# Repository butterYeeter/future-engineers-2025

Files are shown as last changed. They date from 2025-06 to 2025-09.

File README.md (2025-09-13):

# Future Engineers 2025

Welcome to T.M.F.E.'s github for 2025

## A photo of the team with their robot:

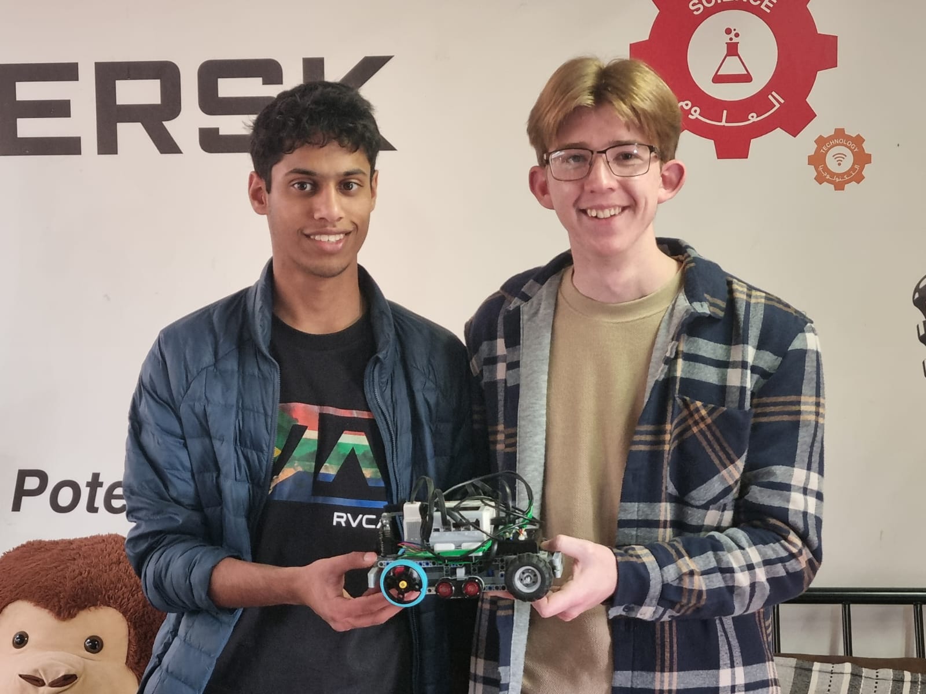
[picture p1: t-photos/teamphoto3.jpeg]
Team Photo


---

## 👥 Team Information

- **Team Name:** T.M.F.E (Trust Me I'm a Future Engineer)
- **Team Members:** Raaid, Josua, HueBert the robot

---

## 📑 Contents

* 🚗 [**Mobility Management**](#-mobility-management)
    * 🛠️ [Chassis Design](#️-chassis-design)
    * 📷 [Camera Position](#-camera-position)
    * 🚦 [Color Sensor Position](#-color-sensor-position)
    * 🧭 [Gyro Sensor Position](#-gyro-sensor-position)
    * ⚙️ [Motor Selection](#️-motor-selection)
* 🔋 [**Power & Sense Management**](#-power--sense-management)
    * 🔌 [Power Management](#-power-management)
    * 👀 [Sense Management](#-sense-management)
* 🚧 [**Obstacle Management**](#-obstacle-management)
    * 🖲️ [Sensor Polling](#-sensor-polling)
    * 🎯 [Steering Control](#-steering-control)
    * 👁 [Detection Method](#-detection-method)
    * 🔀 [Bypassing Obstacles](#-bypassing-obstacles)
    * 🧱 ["L"-shaped turn](#-l-shaped-turn)
    * 🅿️ [Parking](#🅿️-parking)
* 📸 [**Pictures**](#-pictures)
    * 🤖 [Robot Photos](#-robot-photos)
    * 👥 [Team Photos](#-team-photos)
* 🎥 [**Performance Videos**](#-performance-videos)
* 📝 [**Evaluation for Future Development**](#-evaluation-for-future-development)
    * 🤖 [Hardware Evaluation](#-hardware-evaluation)
    * 💾 [Software Evaluation](#-software-evaluation)
* ☎ [**Contact Us**](#-contact-us)
---

## 🚗 [Mobility Management](#-contents)

### 🛠️ [Chassis Design](#-contents)

- **Materials / Kits Used:**
    
    Our robot design consist mostly of original LEGO parts from the EV3 set, in addition to an external Raspberry Pi Pico microcontroller and other electronic sensors. The build instructions including the bill of materials for the LEGO part of the build can be found [here](other/Huebert_Build_Instructions_v1.pdf).
    
    We used LEGO for the construction of the chassis, because it is really easy to build with and modify. For non LEGO parts like the microcontroller circuit and color sensor, we designed and 3D printed LEGO-compatible mounts using black ABS filament to integrate with the robot chassis. The models of these mounts can be found [here](models).
    
- **Design Approach:**
    
    From prior experience, we wanted to have a small and highly maneuverable robot. We started off by listing some requirements. This included minimizing the wheelbase and track width, making the chassis compact and having sharp turning.
    
- **Wheels:** 
    
    We decided on using medium sized wheels,  having wider back wheels for better grip while driving, and thinner wheels to reduce contact area while maintaining friction.

- **Weight Distribution:**
    
    Most of the weight is centered between the front and rear wheels to maintain reliable contact with the mat at any point.
    
- **Component Placement**

    We mounted the raspberry pi on a protoboard and made a 3D printed LEGO compatible mount for it. The mount was designed to fit the robot and not the other way around. We added ports on the protoboard with wires that connect to the various components.
    
- **Steering Geometry:**
    
    Originally we opted for a standard parallel linkage steering mechanism, but when turning sharply found that the front wheels were slipping. We then modified the steering geometry to closely resemble ackermann steering.
    
- **Drivetrain:**
    
    The robot is driven using a LEGO medium motor connected to a differential gearbox system. The resulting gear ratio is 1.4:1.

### 📷 [Camera Position](#-contents)
We used a pixy cam v2 that does obstacle detection for us. 

- **Height & Angle:**
    
    We opted to position the camera on the front of the robot. It was mostly for our convenience in mounting it on the robot where there was space, but we later found it to make our lives more difficult in coding. A future improvement would be to take the angle and position of the camera into account to optimize usage of that glorious 80 degree field of view.
    
### 🚦 [Color Sensor Position](#-contents)
- We used a TCS34725 color sensor board for detecting colors on the mat. The position of the color sensor was carefully determined to maximize the accuracy of the detected colors. To achieve this we placed the color sensor at a specific height above the mat and centered it in the middle of the steering mechanism by designing a custom LEGO compatible mount. This resulted in accurate readings 

### 🧭 [Gyro Sensor Position](#-contents)
- We used an MPU6050 inertial measurement unit as our gyro sensor. The gyro sensor was mounted on a protoboard near the raspberry pi pico to make the wiring easy. We also found that placing the sensor near the center of the robot wasn't necessary due to the size of the robot. 

### ⚙️ [Motor Selection](#-contents)

- **Motor Types:**
    
    We decided on using the LEGO medium motors for both driving and steering.
- **Reason for Choice:**
    
    The LEGO medium motors are already a part of the LEGO brick system and work well with the EV3 controller. They provide a sufficient amount of torque for driving and steering the robot. They also consume less power than the large motors, which significantly increases battery life. They also have a faster speed than the large motors which is beneficial for us since our differential gearbox significantly reduces our speed.
---

## 🔋 [Power & Sense Management](#-contents)

### 🔌 [Power Management](#-contents)
To power our robot, we use a LEGO Li-on battery pack that powers the EV3. All of the LEGO sensors and motors receive power via the ports of the EV3. The Raspberry Pi Pico, is also connected to the EV3 via one of its ports. This port provides power to the Pico. All of the devices connected to the input ports receive +5V while the motors receive up to +9V.

#### **Power Diagram of EV3**
Power distribution

The pico then has it's own regulated 3.3V output that it supply's to the IMU and color sensor. (Wiring diagram for pico and sensors)

- **Core Controller:**
    
    LEGO EV3
- **Secondary Controller:**
    
    Raspberry Pi Pico
- **Battery Type:**
    
    LEGO 2200mAh 7.4V Li-ion battery pack
- **Energy Distribution:**
    
    We use a combination of LEGO cables and custom cables with RJ12 ports to integrate the pi and other sensors with the EV3 brick.
- **Monitoring Features:**
    
    The EV3 screen displays the current battery voltage so we know when it needs to be replaced and recharged.
### 👀 [Sense Management](#-contents)

- **Sensors Used:**
    |Sensor (click for buy link)|Quantity Used|What it looks like|
    |:---|:---:|:---:|
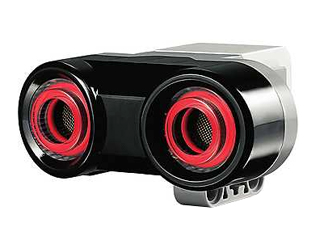
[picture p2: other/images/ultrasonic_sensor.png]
LEGO Mindsorms Ultrasonic Sensor
    [LEGO mindstorms ultrasonic sensor](https://www.bricklink.com/v2/catalog/catalogitem.page?S=45504-1#T=S&O={%22iconly%22:0}) | 2 |
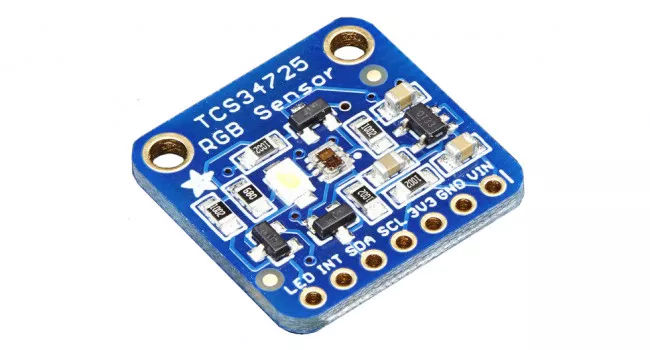
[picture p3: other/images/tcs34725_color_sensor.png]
TCS34725 Color Sensor
    [TCS34725 color sensor](https://www.robotics.org.za/AF1334?search=TCS34725)              | 1 |
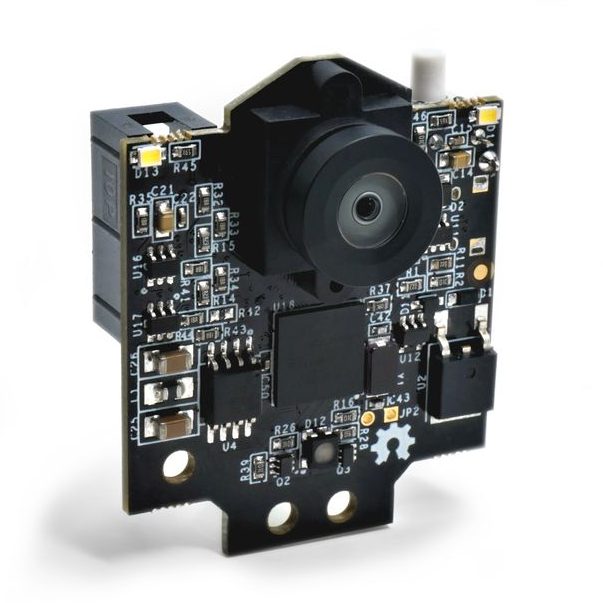
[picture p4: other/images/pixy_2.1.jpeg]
Pixycam 2.1
    [Pixycam 2.1](https://tribotix.com/product/pixycam2-1/)                        | 1 |
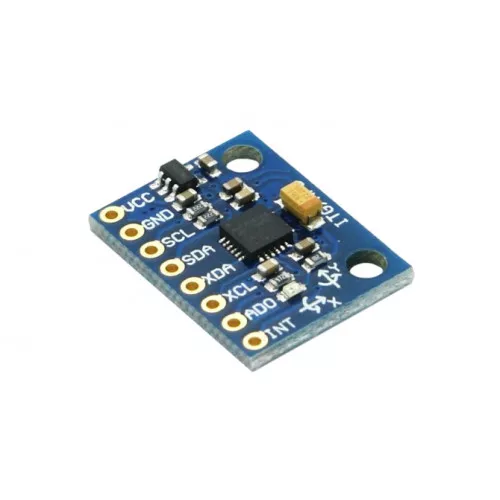
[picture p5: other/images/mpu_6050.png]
MPU 6050
    [MPU 6050 inertial measurement unit](https://www.robotics.org.za/GY-521) | 1 |
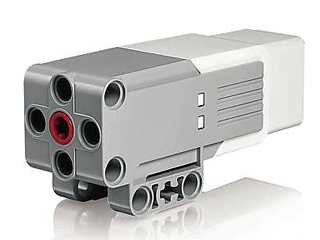
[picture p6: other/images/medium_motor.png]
LEGO Medium Motor
    [Built-in rotary encoders of the LEGO medium motors](https://www.bricklink.com/v2/catalog/catalogitem.page?S=45503-1#T=S&O={%22iconly%22:0})|2|
- **Purpose of Each Sensor:**
    - The **ultrasonic sensors** are used to recenter the robot within each straight section on the mat. We have found that the LEGO ultrasonic sensors' distance values lag behind reality. This means we can't rely on them to detect when to turn for example(by checking for when the inside wall disappears). In future we will probably switch to using time of flight sensors or even a scanning LIDAR.
    
    - The **color sensor** is used to detect the colored lines on the mat to decide when to turn. Initially we used a HiTechnic color sensor however it was quickly found to inadequate. It could not detect the colors in the short amount of time when driving over a line.

        The TCS34725 sensor returns color in the form of RGB. In order to detect orange and blue lines, we convert this color to HSV(Hue, Saturation, Value) and then simply check for a range of values for H, S and V.

        The following algorithm is used to convert RGB to HSV:

        ```C
        // Find min and max component
        float max = r;
        if (g > max) max = g;
        if (b > max) max = b;

        float min = r;
        if (g < min) min = g;
        if (b < min) min = b;

        // Calculate difference between min and max channel
        float delta = max - min;

        float h = 0.0f;
        float s = 0.0f;
        float v = max;
    
        // Determine values for saturation and hue
        if (delta > 0.00001f) {
            s = (max > 0.0f) ? (delta / max) : 0.0f;

            if (max == r) {
                h = 60.0f * ((g - b) / delta);
                if (h < 0.0f) h += 360.0f;
            } else if (max == g) {
                h = 60.0f * (((b - r) / delta) + 2.0f);
            } else {
                h = 60.0f * (((r - g) / delta) + 4.0f);
            }
        }
        ```
        
        Then we check for orange and blue using the following:
        ```C!
        // Check thresholds for blue and orange colors
        if (s > 0.35f && v > 0.6f) {
            // Blue range
            if (h >= 200.0f && h <= 250.0f) {   // Hue range for blue
                return COLOR_BLUE;
            }
        } else if (s > 0.45f && v > 0.7f) {
            if ((h >= 0.0f && h <= 50.0f) || (h >= 340.0f && h <= 360.0f)) {    // Hue range for orange
                return COLOR_ORANGE;
            }
        }
        ```
        
        We did however find that the color sensor is more sensitive to red than it is to blue. So we also needed to do color correction. This is done by first using a white reference(e.g. a piece of paper) and seeing what the raw color values from the sensor is. We then use this raw color to apply a correction using the following algorithm:

        ```python!
      def get_color_corrected(self):
            raw = self.get_color() # Raw color

            # Divide each channel by the corresponding channel in our white reference
            col = [raw[i]/self.white[i] for i in range(3)]

            # Find the maximum component of our color and normalize each channel in range 0..1
            max_component = max(col[0], max(col[1], col[2]))
            norm = [c/max_component for c in col]

            return norm
        
        ```
    
    - The **pixy cam** is used to detect traffic objects in the obstacle challenge. Using the pixy removed the need for us to do the computer vision ourselves. The pixy also provides a convenient interface over I2C to get the objects that it is tracking. We simply configure the camera on a pc via PixyMon to get it to track red and green traffic lights.

        We get the largest block from the pixy cam using the following function:
        ```python !
         # Function that returns the largest detected object
         def get_largest_signature(self):
            # Send command bytes to get the largest block
            cmd = bytes((174, 193, 32, 2, 255, 1))
            self.write(0, cmd)

            # Read in the response packet
            response = self.read(0, 20)

            # Return a dictionary containing the information about the currently detected block.
            return {
              "type":int.from_bytes(response[6:8], 'little'),
              "cx":int.from_bytes(response[8:10], 'little'),
              "cy":int.from_bytes(response[10:12], 'little'),
              "w":int.from_bytes(response[12:14], 'little'),
              "h":int.from_bytes(response[14:16], 'little'),
            }
        ```
        
        We send a command over I2C and receive data from the pixy. The data from the pixy is 5 unsigned shorts in little endian format which we decode according to the pixy documentation.

        During testing, we found that the pixy cam is quite unreliable in varying light conditions. During our research, we found that using [OpenCV](https://opencv.org/) to detect obstacles was far more reliable than the pixy. We believe a future improvement will be to use opencv on a Raspberry Pi.
    
    - The IMU is used to track the robot's absolute angle during the run. We use this sensor to drive in a straight line, make turns around corners and overtake objects.

        Initially one of LEGO's gyro sensors however there it would continuously drift over time. This meant it was highly unreliable. Another issue was that the gyro did not have high angular resolution.
        
        We also considered a HiTechnic compass sensor and this would have fixed our issues. However for a certain range of angles, the compass sensor did not return the correct absolute angle. So this was also quite unreliable.
        
        In the end, we opted for the MPU6050 IMU as it has a much higher angular resolution as well as a high data rate(8000 Hz). The MPU measures angular velocity so in order to get angular position we numerically integrate the data. We also pass the raw angular velocity through a low pass filter to get rid of noise above ~600 Hz in our data. We use the following code:
        
        ```C
        float buf[7];
        mpu6050_read_float(buf);    // Get data from mpu

        // Calculate delta time between loop iterations
        current_time = to_us_since_boot(get_absolute_time());
        float delta_time = (float)(current_time - last_time)/1000000;
        last_time = current_time;
        
        // Apply a low pass filter
        float alpha = delta_time / (RC + delta_time);
        gyro_prev = alpha * buf[6] + (1-alpha) * gyro_prev;
        angle += delta_time * gyro_prev;
        ```
        The following photos show's the gyro data before and after applying a lowpass filter:
        
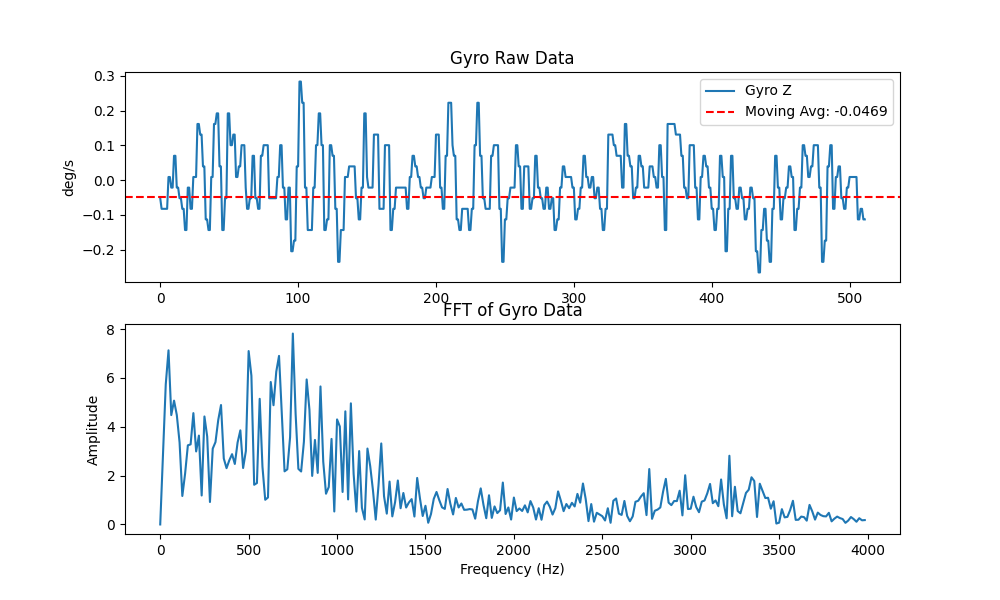
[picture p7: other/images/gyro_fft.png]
Raw Data
        
        
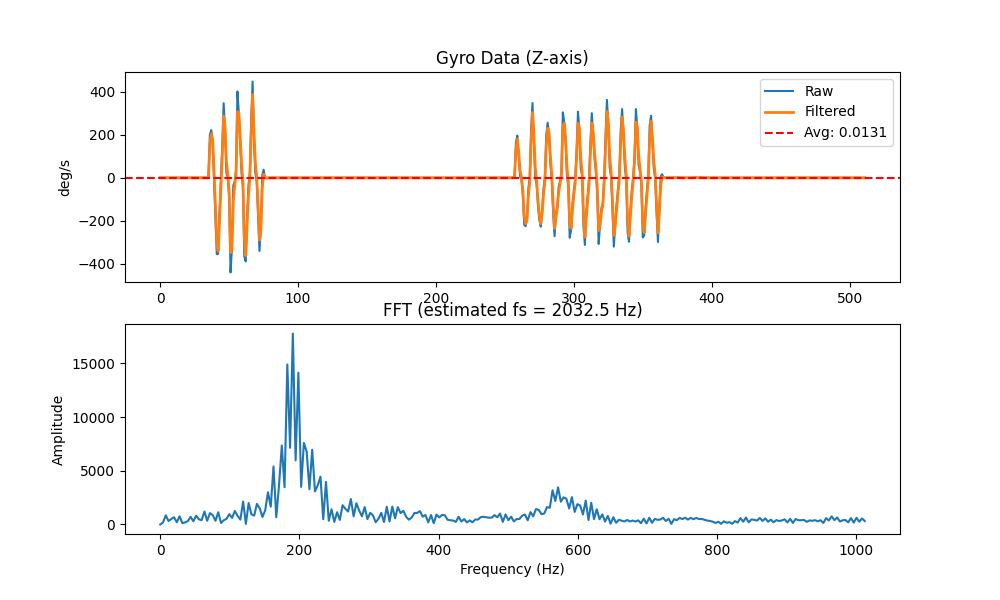
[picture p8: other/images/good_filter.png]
Filtered Data
        

    - The motor's **rotary encoders** are used to drive specific distances based on rotations of the drive motor as well as turn the steering to specific angles. This is done by dividing the distance we want to travel by the circumference of our wheels to get the number of rotations. We then multiply by the gears ratio and multiply by 360 to get degrees:

        ```python
        def distance_to_angle(dist_mm: int):
            # Wheel has 56 mm diameter  
            wheel_diameter = 56
            # PI
            PI = 3.1415926535
            # Gear ratio of our drive motor to wheels is 1.4:1
            gear_ratio = 1.4
            # Return the calculated amount in degrees
            return int(dist_mm / (wheel_diameter * PI) * gear_ratio * 360)
        ```

- **Circuitry:**
    
    The Pixy cam as well as the ultrasonic sensors are connected directly to the EV3 brick via its sensor input ports. The EV3 receives information about detected lines and absolute angle via the Raspberry Pi Pico which is connected on another input port.
    
    #### Wiring diagram of EV3 brick and sensors
    Main wiring diagram of robot

    The Raspberry Pi Pico handles detected colored lines and integrating angular velocity to get absolute angle. The following wiring diagram shows
    how the pico and its sensors receive power
    
    #### Wiring diagram of Raspberry Pi Pico and sensors
    Wiring diagram of sensor board

---

## 🚧 [Obstacle Management](#-contents)

To tackle the obstacle challenge, we first identified a few key scenarios that the robot might encounter during a run. These are: cruising in a straight line at the center of a lane, tracking an object and driving towards it, overtaking an object and finally turning around corners.

We abstracted this way in code by using a state machine architecture. The state machine is in one large while loop. Our obstacle challenge program follow the following procedure:

State machine diagram

Our main states are `CRUISE, TRACK_OBJECT, OVERTAKE and LTURN`. 

We first start by initialing our sensors and motors on their corresponding ports. The gyro is also calibrated by the Pi Pico. It collects 10000 raw gyro samples and averages this to calculate the bias of each gyro axis. We then are in a wait state which continuously loops until the center button is pressed. 

Outside of our main loop, we store some state about the run:
```python
# Current state
state="CRUISE"
# The angle reported by the gyro at the beginning of a run
start_of_round_heading = gyro.get_angle()
# The round direction. We assume CCW by default
challenge_direction = 1
# The direction we'll be facing at the end of the run
end_of_round_heading = challenge_direction * 360 * NUM_LAPS + start_of_round_heading
# Current weight of the gyro PID controller in cruise mode
gyro_weight = GYRO_WEIGHT
# Current weight of ultrasonic PID controller in cruise  mode
us_weight = US_WEIGHT
# The current angle reported by the gyro
angle = gyro.get_angle()
# Variable used to store how many motor rotations are need to overtake an obstacle
motor_angle_target = 0
# The last obstacle we passed
last_obstacle = 0
# Variable to determine the time between detecting colored lines. Used to prevent false positives
last_turn_time = timer.time() - 1500
# The number of turns the robot has made
turns = 0

```

### 🖲️ [Sensor Polling](#-contents)

Then we enter our main program loop. At the beginning each loop iteration we get data from our sensors and calculate `delta_angle`, `lane_width` and `delta_dist`. We also get the detected blocks from the pixy cam and the detected lines from the color sensor. Then we determine whether we need to turn:

```python
# Get gyro angle and calculate our delta from the target angle
angle = gyro.get_angle()
delta_angle = angle - gyro_pid.target

# Get ultrasonic distances and calculate lane_width and delta_dist
right_dist = right_us.distance()
left_dist = left_us.distance()
lane_width = right_dist + left_dist   # Sum of the right and left distance
delta_dist =  right_dist - left_dist        # Difference between right and left distance
abs_delta_dist = abs(dist)        # Absolute value of delta dist

# Ask pixy for the largest detected block
block = pixy.get_largest_block()
# If the pixy detected a block, check if its in a valid x coordinate range
if  block != None:
if block["cx"] > PIXY_MAX_X or block["cx"] < PIXY_MIN_X:
  block = None

# Calculate the time since the last turn and get the detected color
time_since_last_turn = timer.time() - last_turn_time
detected_color = color.get_detected()

# Reset the detected color if less than 4 seconds has passed since the last detection
if time_since_last_turn < 4000:
    detected_color = 0
    color.reset_detected()
 
# Check whether we need to enter the LTURN state to have a better chance of dodging an obstacle
red_lturn = detected_color == ORANGE and last_obstacle == RED_SIG
green_lturn = detected_color == BLUE and last_obstacle == GREEN_SIG

if (red_lturn or green_lturn):
    # Transition to LTURN state
    state = "LTURN"
    
    # Determine the round direction using the detected color
    if turns == 0:
      challenge_direction = 1 if detected_color == BLUE else -1
    
    turns += 1            # Increment turns
elif detected_color != 0:
    # Determine the heading change to turn left or right
    heading_change = LEFT if detected_color == BLUE else RIGHT
    
    # Determine the round direction using the detected color
    if turns == 0:
        challenge_direction = 1 if detected_color == BLUE else -1
        
    # Update the gyro PID target and update the last turn time
    gyro_pid.target += heading_change
    last_turn_time = timer.time()
    turns += 1        # Increment turns
```

### 🎯 [Steering Control](#-contents)

Next we enter an if else block that determines what to do this loop iteration based on the `state` variable. In the `CRUISE` state we use a weighted sum of 2 PID controllers. One uses the gyro to drive straight and one uses the `delta_dist` variable calculated before to center us within a lane. We also dynamically change the weights of the controllers based on `delta_angle`, `lane_width` and `delta_dist`.

```python
# Determine how to change the weights of the PID controllers
if abs(delta_angle) > 32 or lane_width < 400 or lane_width > 1200:
    # If delta_angle is large, the ultrasonic sensors report erroneous data
    # and should not be used. If the lane width is less than 
    # 400 mm (when  passing an object) or if we are in a corner
    # section(lane_width greater than 1200 mm) we should also not rely on the 
    # ultrasonic sensors.
    
    # Comletely deactivate the ultrasonic PID controller
    us_weight = 0
    gyro_weight = 1
elif abs_delta_dist > 200 and abs_delta_dist < 1000:
    # Only favour the the ultrasonic controller when we are far from the center
    #  of the lane to improve obstacle detection.
    us_weight = 0.6
    gyro_weight = 0.4
else:
    # Else set to default weights favouring the gyro controller
    us_weight = US_WEIGHT
    gyro_weight = GYRO_WEIGHT

# If we see a random spike in distance, dampen the ultrasonic controller
if abs(abs_delta_dist) > 1000:
  us_weight *= 0.6

# Calculate the steering command based on our controllers
steer_cmd = gyro_pid.loop(angle) * gyro_weight + wall_pid.loop(delta_dist) * us_weight
set_steer(steer_cmd)
```

### 👁 [Detection Method](#-contents)

In the `CRUISE` state we calculate the area of an object if the pixy has detected a block and transition to the `TRACK_OBJECT` state.

```python
# If we detected a valid block before, check if it meets the minimum area threshold and transition to TRACK_OBJECT state
if block != None:
  area = block["w"] * block["h"]
  state = "TRACK_OBJECT" if area > MIN_BLOCK_AREA_THRESH else "CRUISE"
```

### 🔀 [Bypassing Obstacles](#-contents)

#### Track object

In the `TRACK_OBJECT` state we use the blocks x position(returned by pixy) and use a PID controller to drive towards it. If we lose the object we transition back to the `CRUISE` state. Else, if the area of the detected block is greater than `MAX_BLOCK_AREA` we transition to the `OVERTAKE` state.

```python
# If we lost the block, transition to CRUISE state
if block == None:
  state = "CRUISE"
  continue

# Calcualte area of block and use it to determine how strongly we should
# track the object
area = block["w"] * block["h"]
pixy_weight = 1 if area > 1800 else 0.45

# Calculate the steering command
steer_cmd = pixy_pid.loop(316-block["cx"]) * pixy_weight
set_steer(steer_cmd)

# Use the area of the detected object bounding box as a metric for distance
# to the object and determing whether we should overtake.
if  area > MAX_BLOCK_AREA:
    # Play an audio cue to indicate which color object we're overtaking
    if block["type"] == RED_SIG:
        brick.speaker.beep(duration=200)
    else:
        brick.speaker.beep(650, 200)

    # Determine the overtake direction
    state = "OVERTAKE-RIGHT" if block["type"] == RED_SIG else "OVERTAKE-LEFT"

    # If we are at a sharp angle relative to object, increase the overtake distance
    distance = 215 if abs(delta_angle) < 40 else 240
    motor_angle_target = drive_motor.angle() + distance_to_angle(distance)

    # Set the last obstacle dodged to the current obstacle
    last_obstacle = block["type"]

    # Determine the change in heading to overtake the object
    if state.endswith("RIGHT"):
        gyro_pid.target = (gyro_pid.target if delta_angle < 0 else angle) -45
    else:
        gyro_pid.target = (gyro_pid.target if delta_angle > 0 else angle) +45
```

#### Overtake

Once we enter the `OVERTAKE-` state, we drive for the calculated `motor_angle_target` using the gyro PID and transition back to the `CRUISE` state once that is complete.

```python
# Calculate steering command
steer_cmd = gyro_pid.loop(angle)
set_steer(steer_cmd)

# OVERTAKE completed
if drive_motor.angle() > motor_angle_target:
    state = "CRUISE"
```

### 🧱 ["L"-shaped turn](#-contents)

#### Inside state machine

Finally we have the `LTURN` state that can be entered from the `CRUISE` or `TRACK_OBJECT` states. We simply call a function to perform the maneuver. Then transition back to the `CRUISE` state.

```python
# Determine the direction of the "L"-shaped turn and call the l_turn function
dir = 1 if detected_color == BLUE else -1
l_turn(dir)

# Go back to CRUISE state
state = "CRUISE"
# Reset the detected color
color.reset_detected()
# Set last_turn_time to the current time
last_turn_time = timer.time()
```

#### Function definition

And the maneuver is performed like this:

```python
def l_turn(dir):
    timer = StopWatch()
    set_drive(75)

    # Drive one meter forward to ram into the wall for consistent
    # positioning
    distance = drive_motor.angle() + distance_to_angle(1000)
    while drive_motor.angle() < dist:
        # Calculate steer command
        angle = gyro.get_angle()
        steer_cmd = gyro_pid.loop(angle)
        set_steer(steer_cmd)

    # Determing what direction we need to face based on dir variable
    gyro_pid.target += dir * 90
    set_drive(-75)
    
    # Reverse backwards and face our new 
    # Fowards direction
    while abs(angle - gyro_pid.target) > 2.0:
        # Calcualte steer command
        angle = gyro.get_angle()
        steer_cmd = -gyro_pid.loop(angle)
        set_steer(steer_cmd)

    # Ram into the wall behind us to have enough space to dodge
    # the next obstacle
    start = timer.time()
    while timer.time() - start < 2000:
        # Calculate steer command
        angle = gyro.get_angle()
        steer_cmd = -gyro_pid.loop(angle)
        set_steer(steer_cmd)
    
    # Reset forwards driving speed
    set_drive(75)
```

### 🅿️ [Parking](#-contents)

The robot exits and enters the parking bay by using a fixed parking routine. It starts the obstacle challenge run by exiting the parking bay and ends it by parking the robot parallel to the wall.
#### Parking Detection

After the robot has completed its final lap it starts following the outer wall at a close distance using the outer ultrasonic sensor, keeping straight with the assistance of the gyro sensor. It then looks for two large jumps in the measured distance before entering the parking maneuver. 

---

## 📸 [Pictures](#-contents)

### 🤖 [Robot Photos](#-contents)
Here are pictures of our robot, HueBert:

**Top View:**
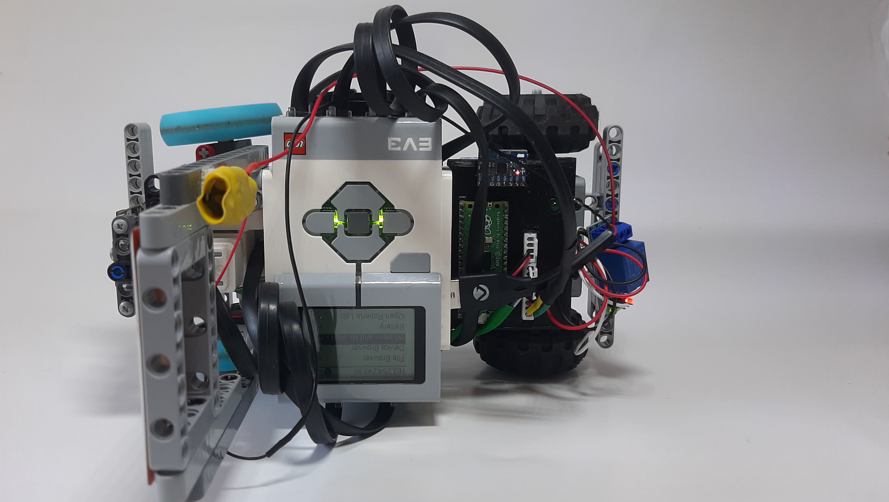
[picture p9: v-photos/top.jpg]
Top view of robot


**Front View:**
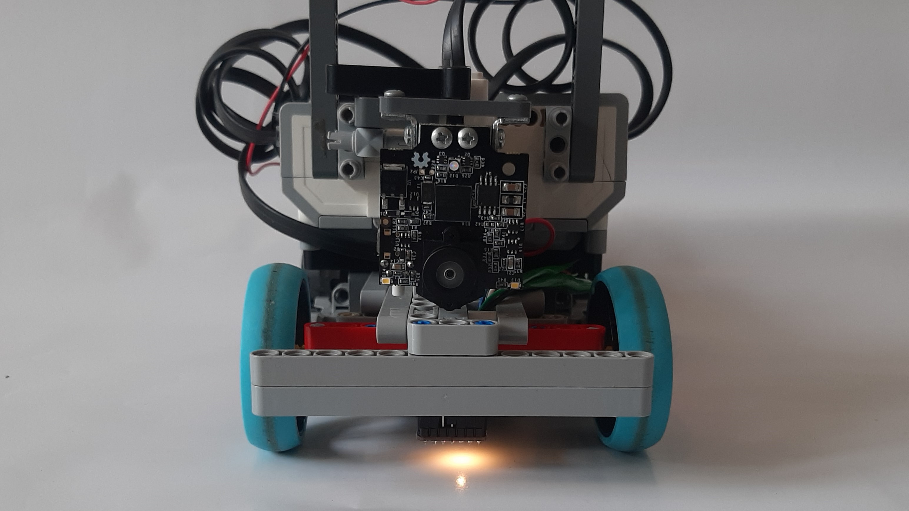
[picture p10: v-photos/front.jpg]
Front view of robot


**Right Side View:**
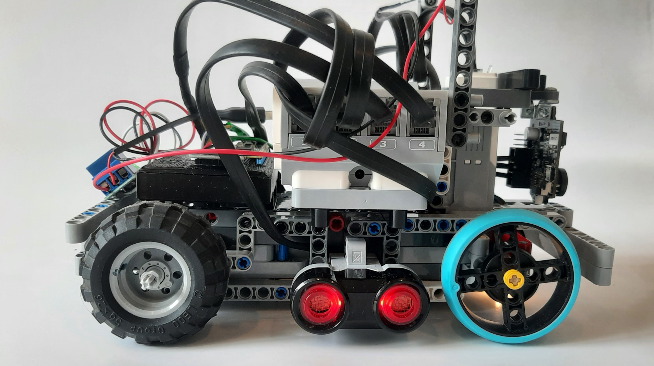
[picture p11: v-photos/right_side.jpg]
Right side view of robot


**Left Side View:**
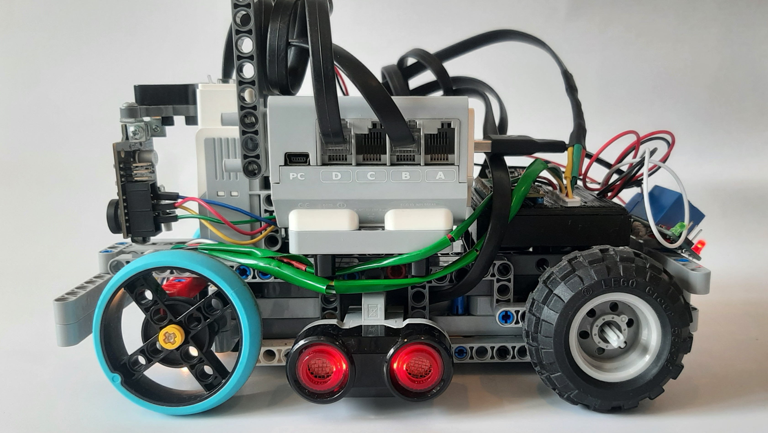
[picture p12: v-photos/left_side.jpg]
Left side view of robot


**Rear View:**
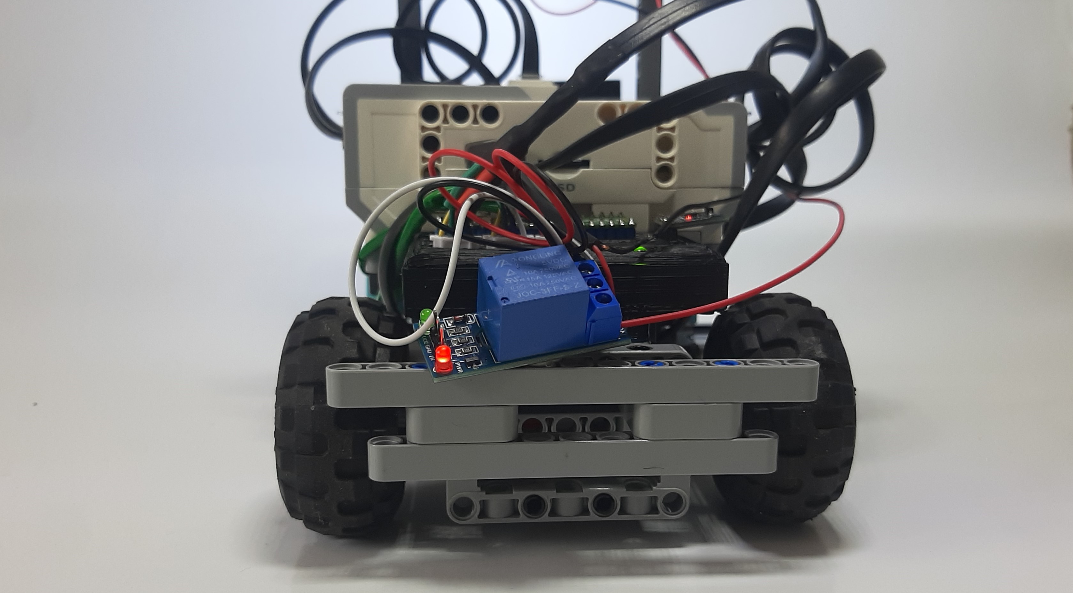
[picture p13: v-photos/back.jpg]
Rear view of robot


**Bottom View:**
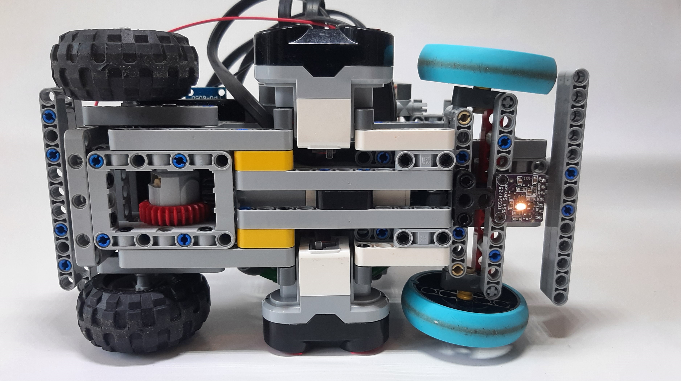
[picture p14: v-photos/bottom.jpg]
Bottom view of robot


### 👥 [Team Photos](#-contents)

**Funny photo**

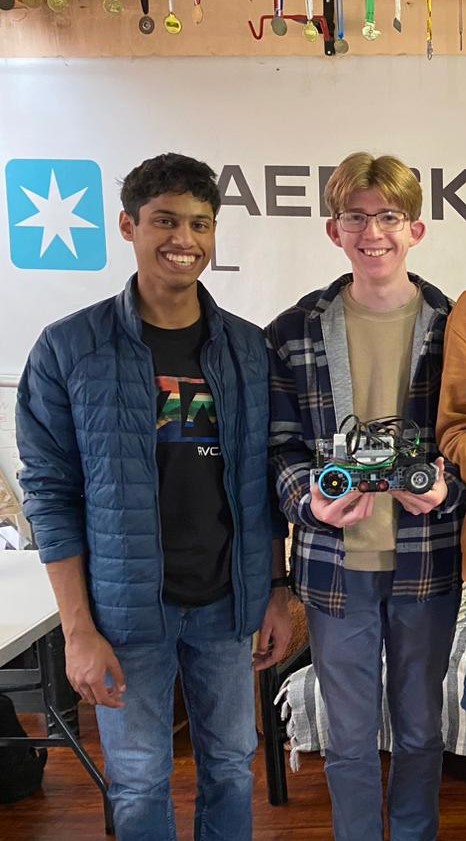
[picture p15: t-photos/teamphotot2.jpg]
very fun picture. Definitely not losing my mind. BEANS


**Serious photo**

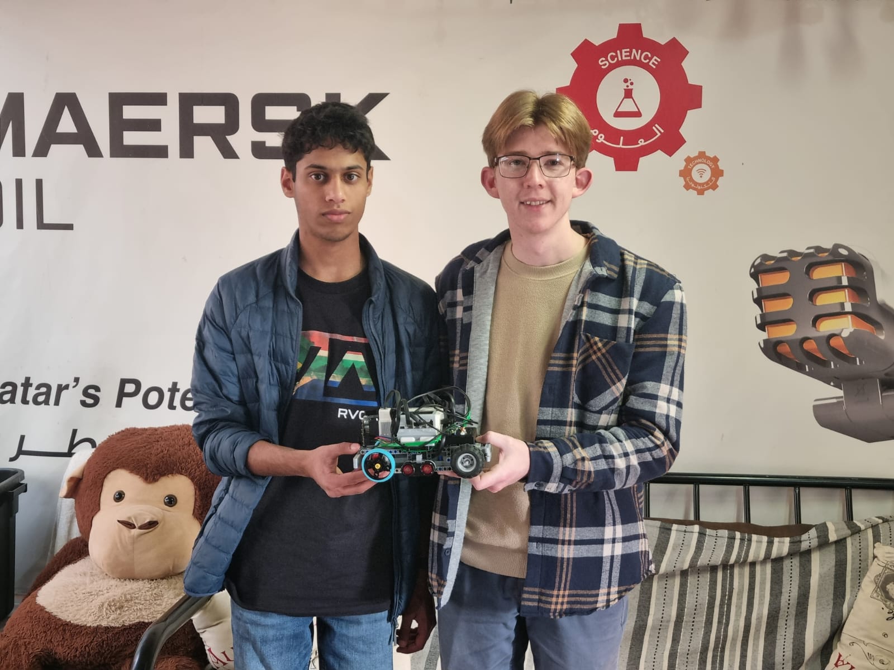
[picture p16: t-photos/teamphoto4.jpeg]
Serious what the sigma


---

## 🎥 [Performance Videos](#-contents)

- **Open Challenge:**
    
    IMAGE ALT TEXT HERE (https://www.youtube.com/watch?v=4Hjj77qfgQk "Click to open with YouTube")
    
- **Obstacle Challenge:**

---

## 📝 [Evaluation for Future Development](#-contents)

This section serves to show our thoughts and reflections of this year's progress and the factors we want to improve on or keep the same in the year(s) to come.
### 🤖 [Hardware Evaluation](#-contents)

- Our current ackermann steering mechanism, although beneficial, is not optimized to minimize friction on the front two wheels. Achieving perfect ackermann steering is definitely a future goal and would enable even tighter steering.

- The Camera mounting position is not optimizing the use of the camera's full field of view. In the future we will look into placing the camera at a better angle.

- The chassis does not provide adequate spacing for managing cables. In the future we will try to keep cable management in mind when we improve our design.

- Although the pixycam works well in most environments and use cases, it falls short in many aspects when compared to pure computer vision approaches. We have found the lack of setting controls disturbing and will thus be switching to a higher quality camera module in the future. 

- The ultrasonic sensors work well on our robot, but they become slow when driving at higher speeds. Because they lag behind the robot's motion they become unreliable. In the future we will be switching to time of flight sensors instead to hopefully fix this issue.

- The EV3 brick is a great microcontroller to start with, but for doing advanced computer vision something more powerful like a raspberry pi would be necessary.
### 💾 [Software Evaluation](#-contents)

- In future we want to continue running our software using python. However we will use a full blown Raspberry Pi. 

- We want to decouple the sensor code from the logic for the challenge. This would allow someone to use alternative sensors and motors to the current setup and reuse the logic. We could simply provide our implementation of sensor classes and define a spec for that others need to implement

- We could use an event driven architecture instead of just a state machine. This would allow us to have different event handlers. It would act in a similar way to the current setup however the user could completely change the robot setup(using different sensors to us such as lidar) and simply modify a config file. The program would then select the appropriate event handlers based on the config file and essentially "glue" parts together to create the program flow.

- We can improve obstacle detection by using a custom computer vision library such as OpenCV rather than relying on the pixy cam's algorithms.

- We can design our strategy/approach to the challenge before implementing software.

## ☎ [Contact Us](#-contents)
|bezjosua@gmail.com|fajandarraaid@gmail.com|
|:---:|:---:|

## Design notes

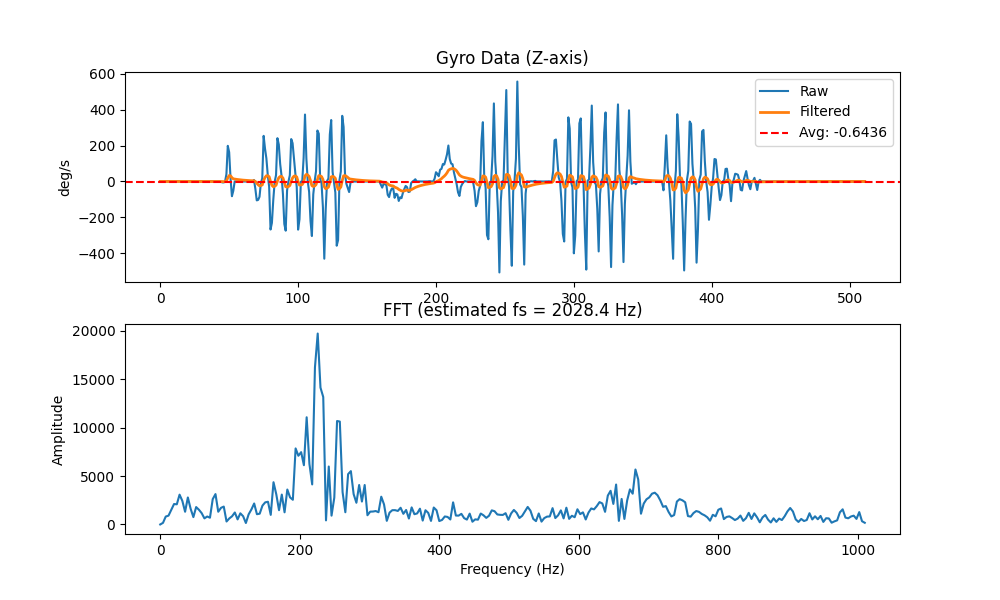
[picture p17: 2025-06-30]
other/images/bad_filter.png

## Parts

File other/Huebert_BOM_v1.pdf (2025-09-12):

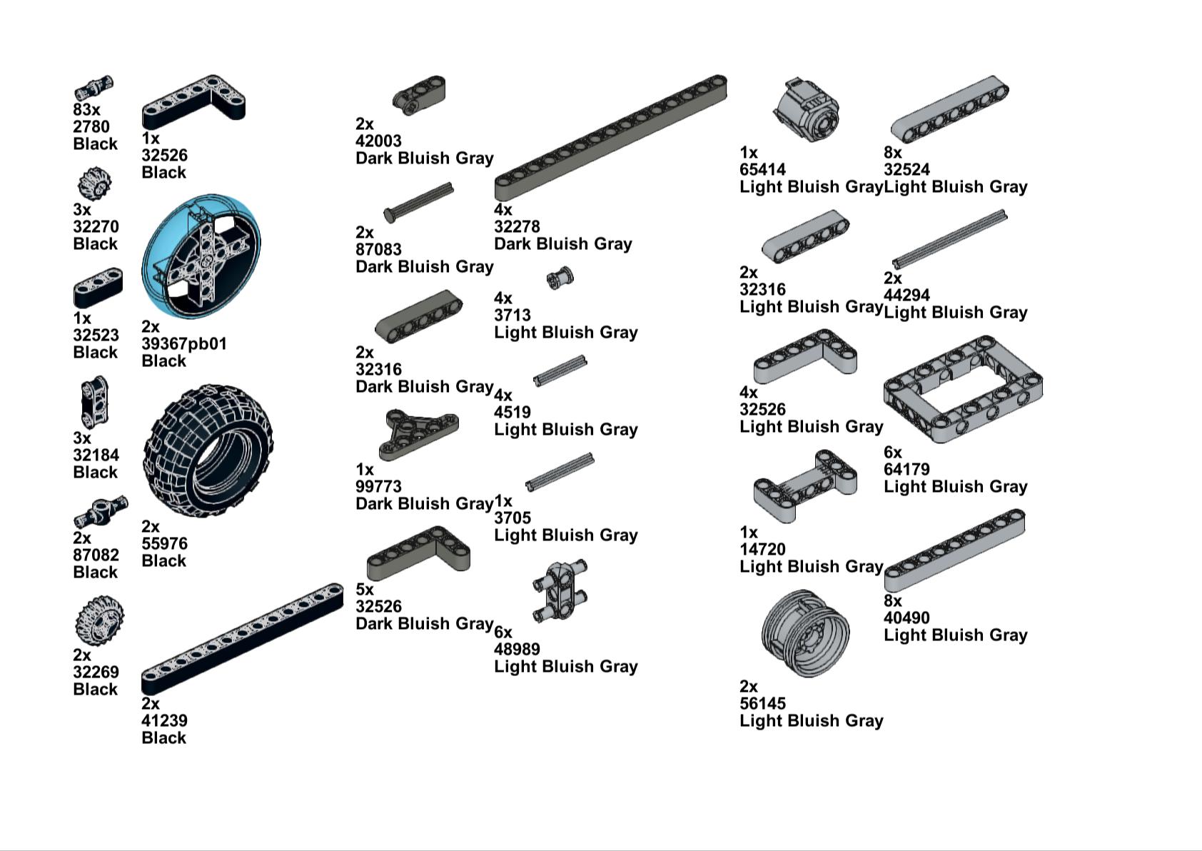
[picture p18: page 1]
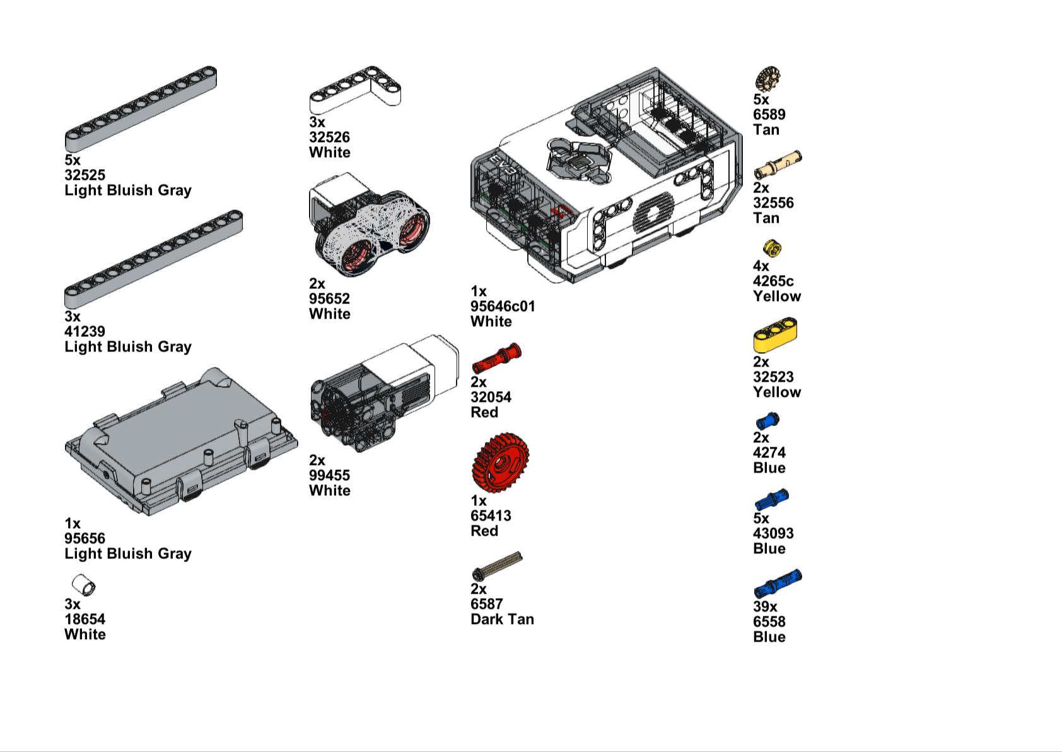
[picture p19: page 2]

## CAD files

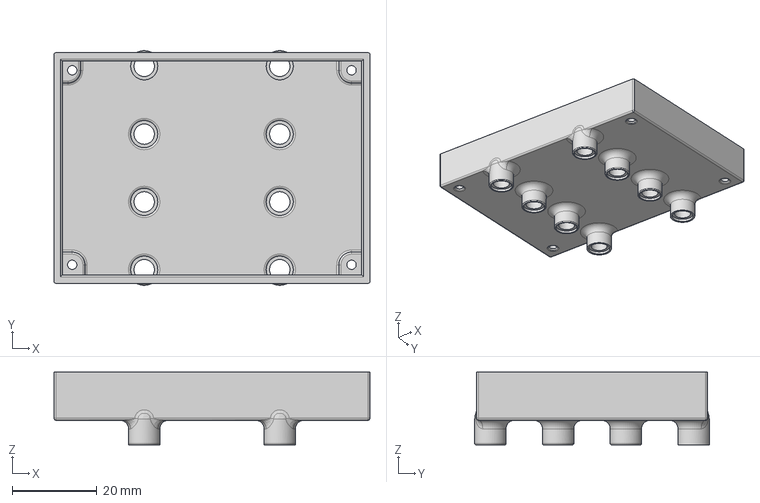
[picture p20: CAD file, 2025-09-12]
models/pcb_mount_box.step
74.6 x 55.4 x 17.2 mm

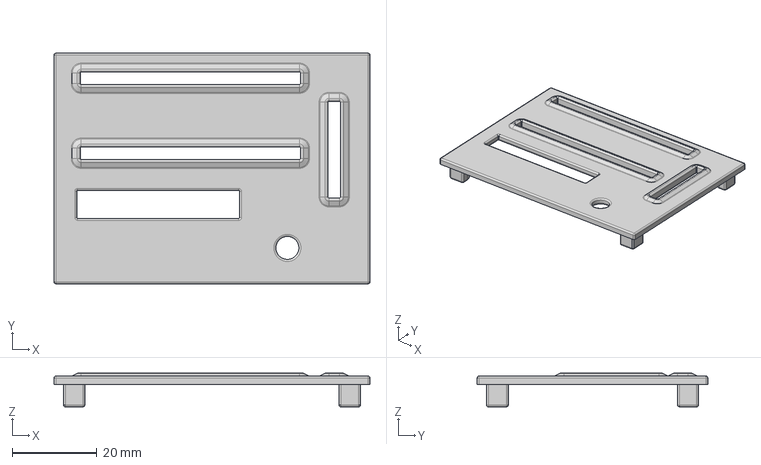
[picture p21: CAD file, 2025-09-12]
models/pcb_mount_lid.step
74.6 x 54.5 x 7.99 mm

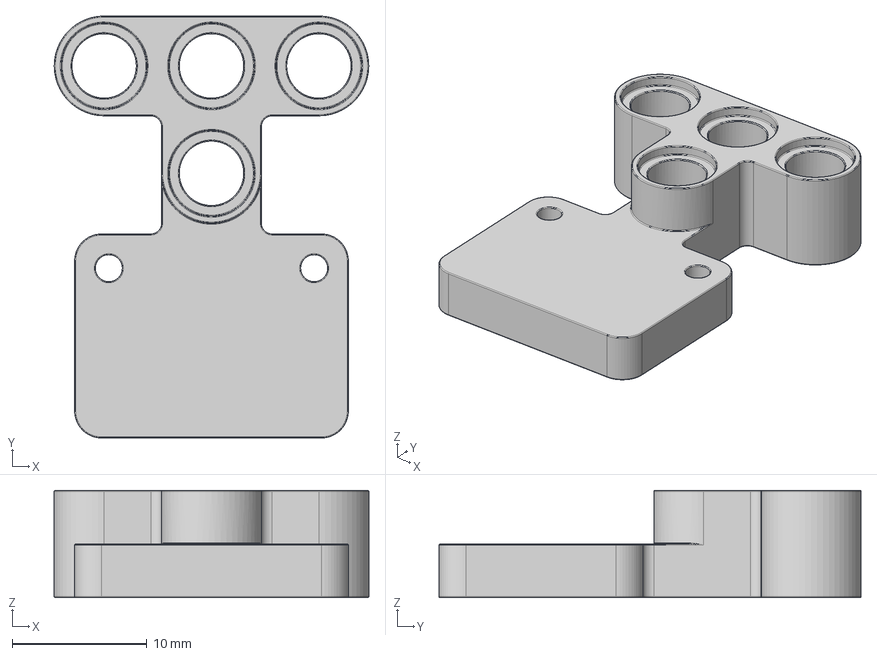
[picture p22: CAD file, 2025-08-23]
models/color_sensor_mount.step
23.4 x 31.3 x 7.97 mm

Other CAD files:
models/color_sensor_mount.stl
models/pcb_mount_box.stl
models/pcb_mount_lid.stl

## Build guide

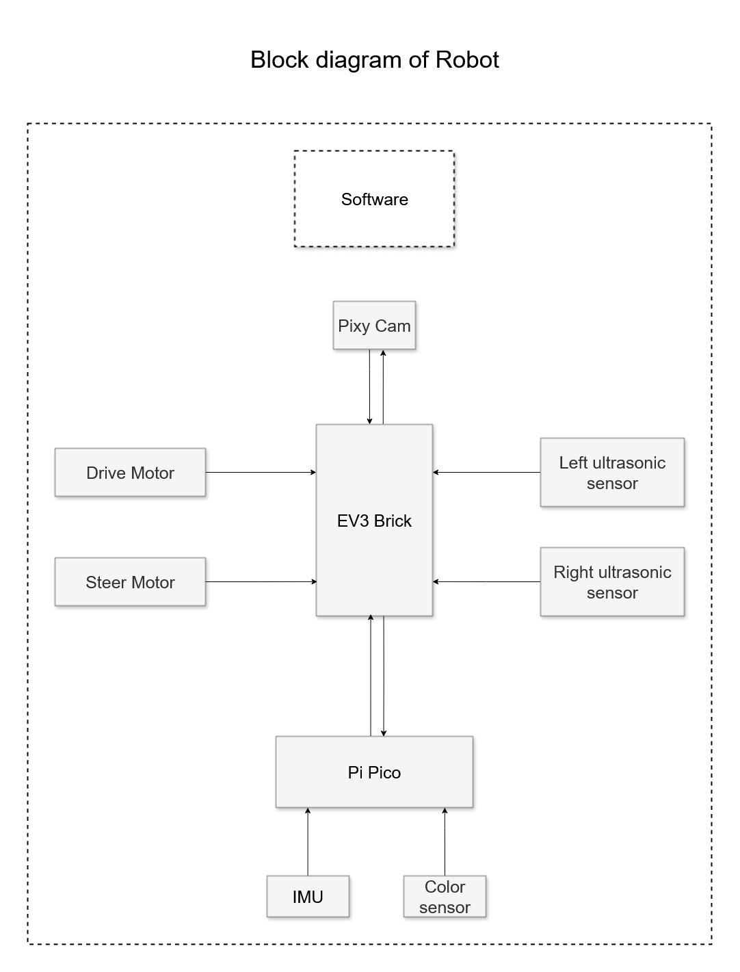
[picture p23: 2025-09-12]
other/images/ev3wiring.png

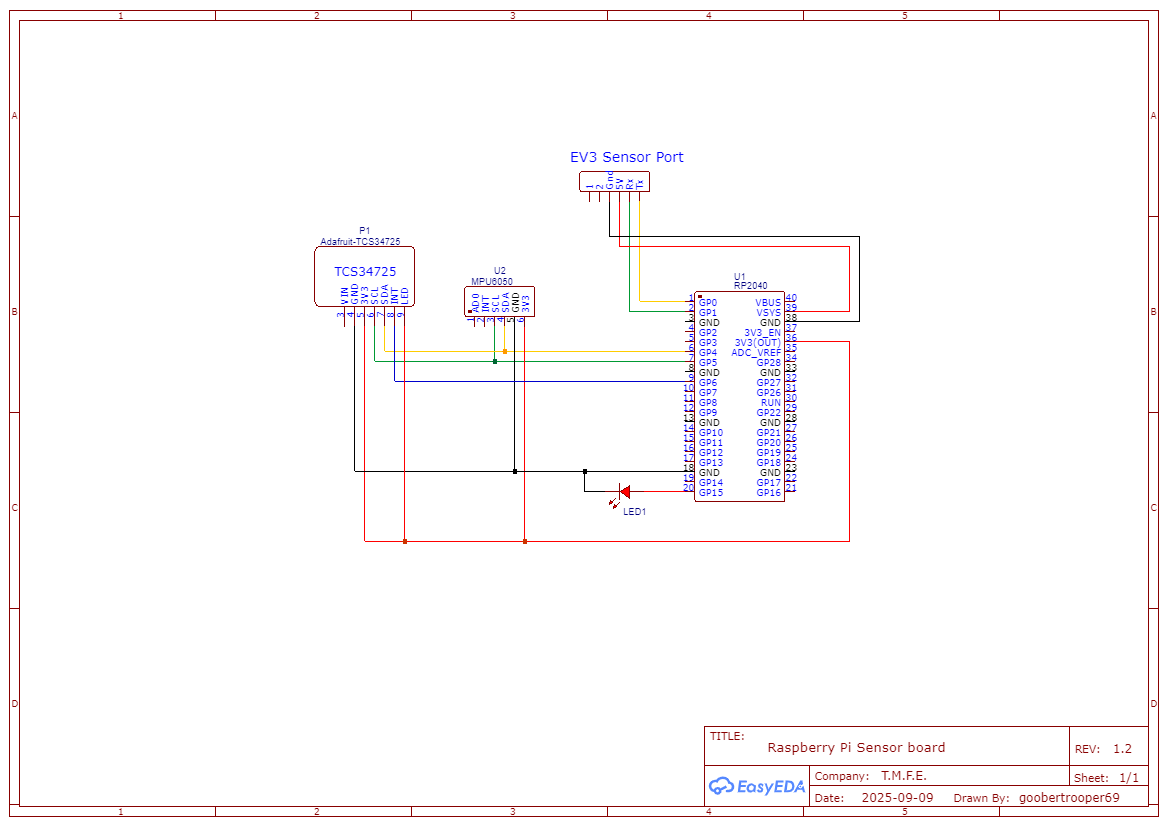
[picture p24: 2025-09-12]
other/images/picowiring.png

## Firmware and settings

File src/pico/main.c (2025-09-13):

#include <stdio.h>
#include "pico/stdlib.h"
#include "hardware/i2c.h"
#include "mpu6050.h"
// #include "qmc5883.h"
#include "tcs34725.h"
#include "math.h"
#include "util.h"

#define GET_ANGLE 'a'
#define CALIBRATE 'g'
#define RESET_ANGLE 'r'
#define GET_COLOR 'c'
#define GET_DETECTED 'd'
#define RESET_DETECTED 'e'
#define LAMP_ON 'l'
#define LAMP_OFF 'o'

#define LAMP_PIN 20

float bi[] = {-43.924241, 12.448210, -73.133957};
float A[3][3] = {{1.096529, -0.033064, -0.055229},
                {-0.033064, 0.989653, -0.120042},
                {-0.055229, -0.120042, 0.819875}};

float white_reference[] = {0.4583333432674408, 0.3333333432674408, 0.25};

void apply_calib(float buf[3]) {
  float tmp[3] = {buf[0] - bi[0], buf[1] - bi[1], buf[2] - bi[2]};

  for (int i = 0; i < 3; i++) {
    buf[i] = A[i][0] * tmp[0] + A[i][1] * tmp[1] + A[i][2] * tmp[2];
  }
}

int main()
{
    stdio_init_all();

    i2c_init(MPU_I2C_PORT, 400000);
    i2c_init(TCS_PORT, 400000);
    
    gpio_set_function(MPU_I2C_SDA, GPIO_FUNC_I2C);
    gpio_set_function(MPU_I2C_SCL, GPIO_FUNC_I2C);
    gpio_pull_up(MPU_I2C_SDA);
    gpio_pull_up(MPU_I2C_SCL);

    gpio_set_function(TCS_SDA, GPIO_FUNC_I2C);
    gpio_set_function(TCS_SCL, GPIO_FUNC_I2C);
    gpio_pull_up(TCS_SDA);
    gpio_pull_up(TCS_SCL);

    gpio_init(25);
    gpio_set_dir(25, GPIO_OUT);
    gpio_init(15);
    gpio_set_dir(15, GPIO_OUT);
    gpio_init(LAMP_PIN);
    gpio_set_dir(LAMP_PIN, GPIO_OUT);
    gpio_put(LAMP_PIN, true);

    gpio_init(TCS_INT);
    gpio_set_dir(TCS_INT, GPIO_IN);
    gpio_pull_up(TCS_INT);

    printf("INIT MPU\n");
    gpio_put(25, true);
    mpu6050_init();
    sleep_ms(3000);

    printf("CALIBRATE GYRO\n");
    gpio_put(25, false);
    mpu6050_calibrate(10000);
    gpio_put(25, true);

    printf("TCS_INIT\n");
    sleep_ms(2000);

    tcs_init();

    uint64_t last_time, current_time;
    current_time = to_us_since_boot(get_absolute_time());
    last_time = current_time;
    uint64_t last_print = current_time;

    float angle = 0.0f;         // Integrated angle using gyro
    float gyro_prev = 0.0f;     // Previous value for apply low pass filter
    float RC = 0.000265f;       // Filter out noise above ~600HZ
    // float color[3];
    volatile int32_t detected_color = COLOR_UNKNOWN;
    bool reset_detected = true;
    while (true) {
        float buf[7];
        mpu6050_read_float(buf);

        // Calculate delta time between loops
        current_time = to_us_since_boot(get_absolute_time());
        float delta_time = (float)(current_time - last_time)/1000000;
        last_time = current_time;
        
        float reg[3];
        tcs_get_rgb(reg);

        detected_color = (reset_detected == true) ? detect_color(reg, white_reference) : detected_color;
        if (detected_color != COLOR_UNKNOWN)
            reset_detected = false;


        // Low pass filter
        float alpha = delta_time / (RC + delta_time);
        gyro_prev = alpha * buf[6] + (1-alpha) * gyro_prev;
        angle += delta_time * gyro_prev;

        // Non blocking input check
        int c = getchar_timeout_us(0);

        // Send current angle if ev3 requests it
        switch (c) {
            case GET_ANGLE:
            // uart_write_blocking
                stdio_put_string((char*)&angle, sizeof(float), false, false);
                bool state = gpio_get(25);
                gpio_put(25, state ^ true);
                break;
            case GET_DETECTED:
                int32_t temp = detected_color;
                // printf("DETECTED %d\n", temp);
                stdio_put_string((char*)&temp, sizeof(int32_t), false, false);
                break;
            case CALIBRATE:
                uint8_t num_samples = getchar_timeout_us(100);
                mpu6050_calibrate(num_samples * 100);
                break;
            case RESET_ANGLE:
                angle = 0.0f;
                break;
            case GET_COLOR:
                float rgb[3];
                tcs_get_rgb(rgb);
                stdio_put_string((char*)rgb, 12, false, false);
                break;
            case RESET_DETECTED:
                // detected_color = COLOR_UNKNOWN;
                reset_detected = true;
                break;

            case LAMP_ON:
                gpio_put(LAMP_PIN, true);
                break;
            case LAMP_OFF:
                gpio_put(LAMP_PIN, false);
                break;
        }

        if (current_time - last_print > 500000) {
            bool state = gpio_get(15);
            gpio_put(15, state ^ true);
            last_print = current_time;
        }
        
        sleep_us(400);
        // printf("Angle: %.2f\n", angle);
    }
}

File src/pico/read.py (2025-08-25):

import serial
import struct
import time

ser = serial.Serial('COM10', baudrate=115200)

angle = 0

ser.reset_input_buffer()
def get_values(num):
  for i in range(num):
    ser.write('a'.encode())
    val = struct.unpack('<f', ser.read(4))[0]
    print(val)
    time.sleep(0.05)

def get_col():
  ser.write('c'.encode())
  val = struct.unpack("<fff", ser.read(12))
  print(f"{val[0]:.8f}, {val[1]:.8f}, {val[2]:.8f}")
  time.sleep(0.1)

def get_det():
  ser.write('d'.encode())
  # print(ser.readline())
  data = ser.read(4)
  val = struct.unpack("<i", data)[0]
  ser.write('e'.encode())
  print(f"DATA: {data}, DETECTED COLOR: {val}")



while True:
  # get_col()
  get_det()
  time.sleep(0.5)
  # get_values(1)

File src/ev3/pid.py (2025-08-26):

# PID Controller Class

class PIDController:
    def __init__(self, target, Kp=1.0, Ki=0.0, Kd=0.0, output_limit=40, integral_limit=100):
        # Controller state
        self.target = target    # Value to maintain
        self.integral = 0
        self.last_error = 0
        
        # Controller gains
        self.Kp = Kp
        self.Ki = Ki
        self.Kd = Kd

        # Limit the controller output range and integral limit
        self.output_limit = output_limit
        self.integral_limit = integral_limit

    # Function that gets called every loop interation to update our controller state,
    # and output a correction
    @micropython.native
    def loop(self, current_value):
        # Calculate new state(error, integral, derivative)
        error = self.target - current_value
        derivative = error - self.last_error
        self.last_error = error
        new_integral = self.integral + error

        # Our unclamped correction
        correction_unclamped = (
            self.Kp * error +
            self.Ki * new_integral +
            self.Kd * derivative
        )

        # Clamp the correction within limits
        correction = max(min(self.output_limit, correction_unclamped), -self.output_limit)

        # If our clamped correction equals the unclamped(i.e. we are within limits), 
        # update our integral state
        if correction == correction_unclamped:
            self.integral = new_integral

            self.integral = max(min(self.integral, self.integral_limit), -self.integral_limit)

        return correction

    def set_target(self, value):
        self.target = value

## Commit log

2025-06-21 PID controller
    Attemping to use a PID controller to drive in a straight line using ultra sonic sensor
2025-06-21 Working PID
    After a few hours of messing around I wasn't able to get a PID controller working. The issue was that the we would set a target angle for the steering motor to try to reach. This worked if the steering correction factor was small.
    However if a very large correction factor was calculated, this would cause the steering motor to stop accepting commands because it woudl try and reach an impossible target angle. This was fixed by using the Motor.track_target() functon.
2025-06-21 Slight tuning and more button options
2025-06-23 Evaluating Sensors
    We have spend a few hours testing ultra sonic and color sensors for
    determining when nto turn. We have also switched the compass for a gyro
    as it makes the dirving code simpler(we don't have to account for the
    wrap around from 359 degrees to 0)
    We logged the data over a few different test runs to test the reliablity
    of the navigation using ultrasonics. We found that sometimes the ultra
    sonic detects erroneous distance readings. Our working theory is that
    this is caused by the geometery of the walls of the course(corners).
    We have not worked out how to solve this issue. So we decided to
    evaluate the color sensor in its place. We set up a simple function that
    returns the s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
2025-06-24 Success full color detection
    By switching to HSV color space we are now able to reliably detect when we see the color blue and know when to turn
    However is an issue... if we drive faster than a certain speed, we can no longer reliably detect the blue line. This is because we are not able to poll the color sensor fast enough
2025-06-28 Testing Gryo
    Pi Pico speaks to mpu6050 gyro and prints the z axis gyro value and the delta time. Python script reads this in over serial and integrates to get the current angle. Drift is very very minimal. However it can still even be improved by doing the integration on the pi pico and the only sending the current angle when a command comes in over serial.
    [main.c, mpu6050.c, mpu6050.h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]
2025-06-28 Angle calculation transfer
    Angle heading calculations have been moved over to the pi pico.In addition to this the pico doens't continously send the data over serial(slow). Data is only transfered when a control character is detected via a input buffer callback. This helps reduced errors of integration.
    [main.c, mpu6050.c, mpu6050.h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]
2025-06-28 Implemented Magnetometer driver
    Wrote a driver for the QMC5883L 3 axis magnetometer and wrote a python script to log data. Used the log data in the magneto 1.2 software to caluclate soft and hard iron calibrations. The data closely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
2025-06-30 Sending data between pico and ev3
    We can now communicate between the ev3 and the pi pico. The ev3 sends the character 'd' and the pico responds with teh curreent angle. We also did an fft plot to see noise in the gyro data
    [fft.py, main.c, mpu6050.c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]
2025-06-30 More FFT analysis
    We upgraded the code that plots the frequency domain for the gyro. From this we were able to determing a good cutoff frequency for gyro noise(roughly 600 Hz). We are using a dynamic lowpass filter on the pico with the RC constant we determined here.
    The 2 plots in the logs folder showcases different cutoff frequencies and the gyro response
    [fft.py]
2025-06-30 Pico to EV3 serial over usb
    Wrote a simple shared library that opens the usb device file /dev/ttyACM0 and reads from and writes to it. This allows us to communicate with the pico on the ev3
    Then used the micropython ffi to call our c functions inside of micropython
2025-06-30 Debug LED
    Added an additional blinking LED in the pico code to verify whether the USB stack has stalled
    Also used python ffi to communicate over the usb port with the pico
    [main.c, read.py]
2025-06-30 Rebase and merge Dev branch
    Cleaning up codebase before restructue
    ================ orignal commit message =================
    Tested using EV3 ultrasonic for driving. The figure in logs folder is showing the gyro drift. Which is very servere over time
2025-06-30 Project restructure
    Restructured the repository to be more inline with what we need for the
    FE comp.
    Also seperated the code in src into 2 directories. One for ev3 and one
    for the pico. This helps with organisation as well as with working on
    the ev3 code.
    Prior to this, the vscode extension we were using was uploading the
    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
2025-07-01 Seperate classes into files
    Organized ev3 source my moving each class into their own file. Also improved the serial comms library and made a gyro class using it.
2025-07-01 Raw bytes
    The pico now responds with the raw bytes reprenting the float rather than a string for performance reaons
2025-07-01 PIDController bug fix
    Fixed a bug in the PIDController class that caused the current value to oscillate around the target value.
    Began working on reimplementing the Actions abstraction
    [pid.py]
2025-07-01 Tuning PID
    Steady state error was observed in the output from the PID controller. The error was between 5 and 10 degrees which is too high.
    We will attempt to use the Ziegler-Nichols method for tuning our controller for QDR damping
2025-07-02 OPEN CHALLENGE :)
    The open challenge has been conquered. Not really difficult task. Just
    setting up our senors and getting the various parts of our robot to work
    together was the challenge.
    Work on the obstacle challenge will now begin. We will first have to
    write a driver to use our pixy2 cam. Shouldn't be too difficult.
2025-07-02 Bug fix
    We no longer return a tuple in the PID function, however the robot class
    still expected it.The only reason we did before was for debugging.
2025-07-12 Basic pixy driver
2025-07-12 Ultrasoinc pid test
2025-07-12 Additional commands for pico
    Started adding addtional commands for the pico such as resetting the
    angle to zero or recalibrating the gyro.
    [main.c]
2025-07-12 Additional commands working
    Reset and calibrate commands now work :)
    [main.c, read.py]
2025-07-12 TCS34725 driver
2025-07-16 Fixed race condition
    Because we were calling i2c functions inside of our interrupt handler, this would cause a context switch. Sometimes this would happen in the middle of an i2c operation using the mpu6050. This would cause the main loop to stall while interrupts continued working
    [main.c, read.py, tcs34725.c]
2025-07-17 Small refactor
    Refactored the gyro class to take in a new USB port class. This allows us to use the same usb port for multiple 'sensors'
2025-07-17 color sensor turning
2025-08-16 Changed communications system
    Switched out the the usb interface for the pico to ev3 communication to
    uart. The pico is now connected to one of the ev3's input ports.
2025-08-16 Updated code to use UART
2025-08-20 Finalized open challenge code and added commments
    The open challenge code is now completed and working.
    Robot can drive 3 laps in both directions and will stop
    in its starting section. There are issues with the UART
    interface when communication between pico and ev3 so we might
    regress to using USB
    Comments was added to every file explaining classes, functions,
    variables as well as certain calculations. This is the beginning of
    documentation
    [color.py, gyro.py, pid.py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]
2025-08-25 Updated color detection code
    Color detection is now done asynchronously on the pico. If the pico detects blue or orange, it stores that until the ev3 tells it to reset the detected color. This prevents the issue of missing the colored lines due to the ev3 logic loop being too slow to poll the color sensor
    [color.py, main.c, read.py]
2025-09-12 Added Build Instructions and BoM for HueBert
2025-09-12 File rename
    Renamed building instructions and BOM pdf for relative linkming in markdown
2025-09-12 Add images for sensors in md
2025-09-12 Pcb Mount Added
    Added model files for the pcb mount
    [pcb_mount_box.step, pcb_mount_box.stl, pcb_mount_lid.step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]
2025-09-13 Update Statemachine flowchart
2025-09-13 Button press
